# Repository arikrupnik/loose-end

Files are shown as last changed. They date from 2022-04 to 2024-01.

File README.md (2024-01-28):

# loose-end: Rocket Glider Research Program

I have a loose end I've been meaning to tie since 2012--a large R/C rocket glider.

Loose End is a family of aircraft.
I use OpenSCAD to define parametric models that can scale from parkflier to giant scale.
A goal of this project is to automate as much of the process as possible to allow for faster iteration of the design.
I use a Makefile to generate individual STLs from the master design, and g-code from the STLs.
Some parts (fins and wing joiner tabs) are in 1.6mm fiberglass (G10); the Makefile generates DXFs for them.

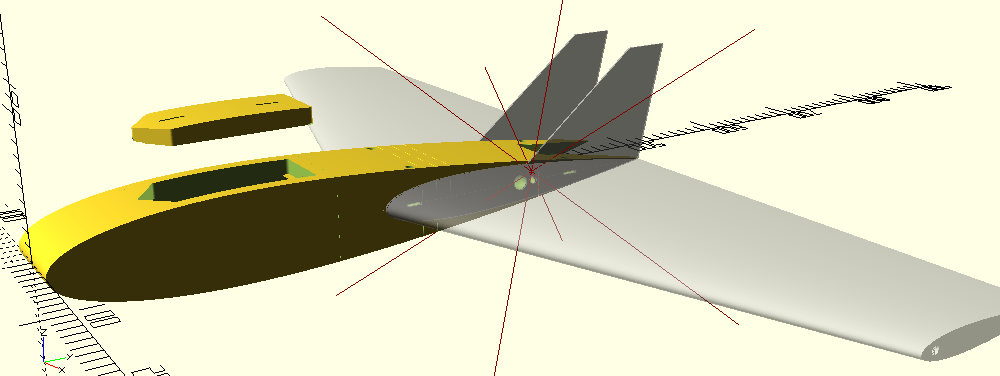
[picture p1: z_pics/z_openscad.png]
OpenSCAD model


Initial versions use off-the-shelf wings from a HobbyKing RadJet800.
This version has a 24mm motor mount.
This version has flown on E9, E15, E6, E20 and F12 motors.
In January 2023, I am designing printable wings.

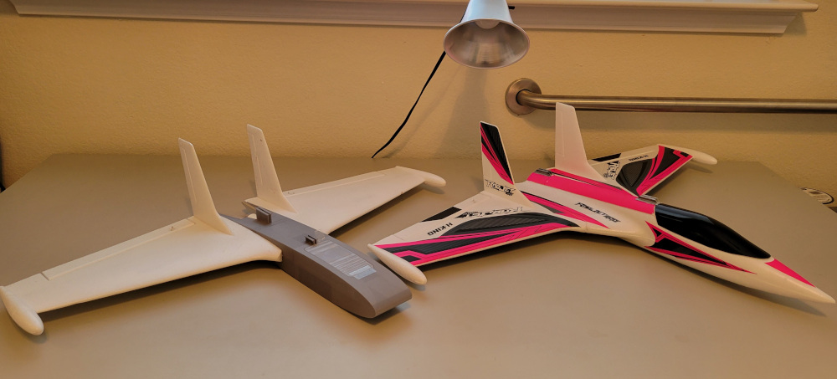
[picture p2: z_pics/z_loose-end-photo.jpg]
Loose End 24 and RadJet800


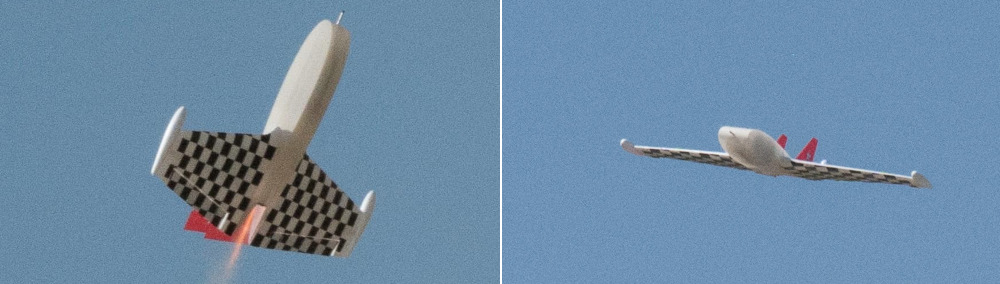
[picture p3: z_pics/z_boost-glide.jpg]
Loose End 24 DW in boost and glide


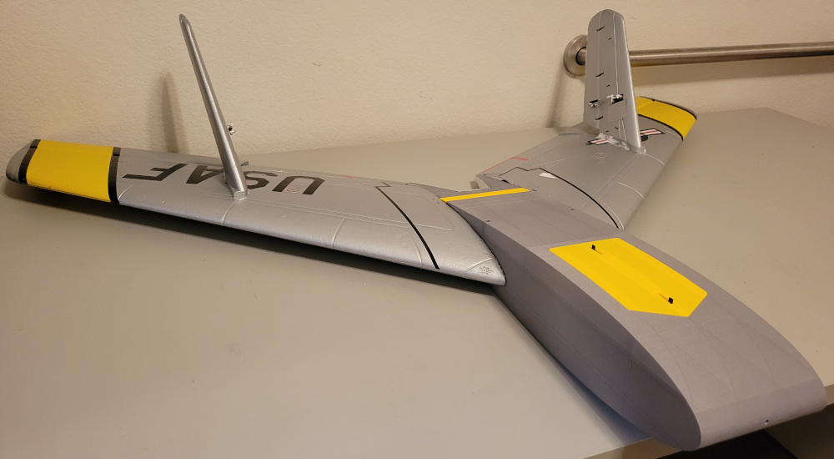
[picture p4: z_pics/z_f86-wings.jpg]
Loose End 29 using Freewing F-86 wings


Fuselage prints upright, in sections.
Most pieces use a single perimeter and 2% infill.
Spar carrythrough (green in the image below) uses 15% infill.
This part allows me to cut wing spar in two and the motor to pass through the wing, similar to mid-wing jet fighters like MiG-21 or F-16.

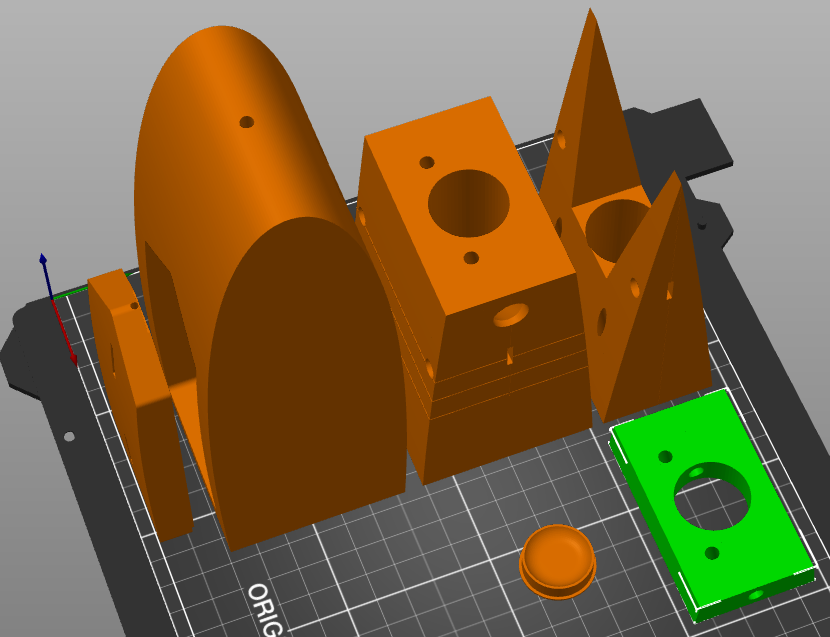
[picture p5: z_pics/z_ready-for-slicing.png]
Ready for Printing


I print these models on a Prusa MK3S+ using Prusament PLA.
I use PrusaSlicer in batch mode: [slicer-config](slicer-config) directory holds the INI files I use.
Key settings are:

* Most parts are single wall:
  * Perimeters: 1
  * Horizontal Shells: top: 3, bottom: 1 (max shell thickness bottom: 0 to force single layer)
  * Infill Density: 2%
  * Infill Pattern: Grid
  * Max Length of Infill Anchor: 0 (with some infill patterns, other values create arbitrarily long anchors; 3mm would be ideal)
  * Filament Extra Length on Retract: 0.1mm (helps avoid gaps between infill and perimeters)
  * Brim: outer, 3mm
* Spar carrythrough:
  * Perimeters: 2
  * Infill Density: 15%
  * Infill Pattern: Grid
  * Brim: outer, 3mm
* MMT plug:
  * Fill Pattern: concentric
  * Top Fill Pattern: concentric
  * Bottom Fill Pattern: concentric
  * Brim width: 0mm (the model has its own shoulder)

I make a new tag (release) when I print a new flying aircraft.
Release notes summarize changes from previous version and actual experience with them.

* January 2024: 29mm version using wings and fins from 80mm Freewing F-86
* October 2022: PLA fuselage, RJ wings, G10 fins
* April 2022: first flights, PLA fulseage, RJ wings and fins

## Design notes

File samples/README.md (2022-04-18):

# samples/: example usage for modules in this project

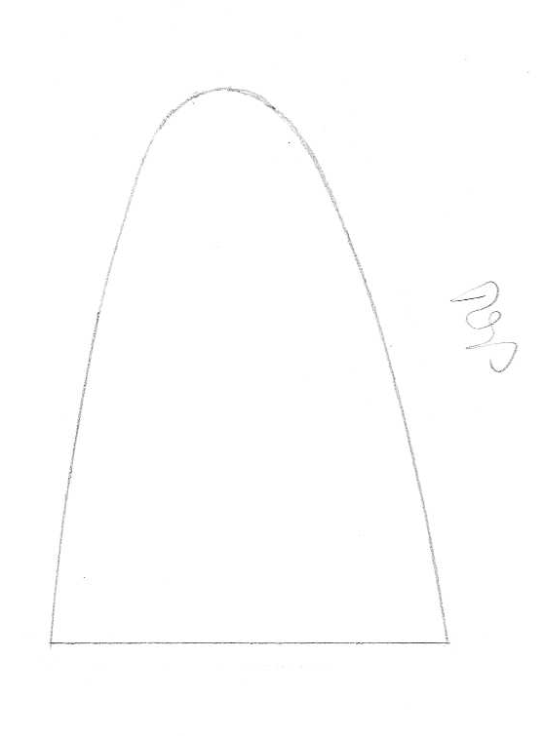
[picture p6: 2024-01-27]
extras/bronco-le.png

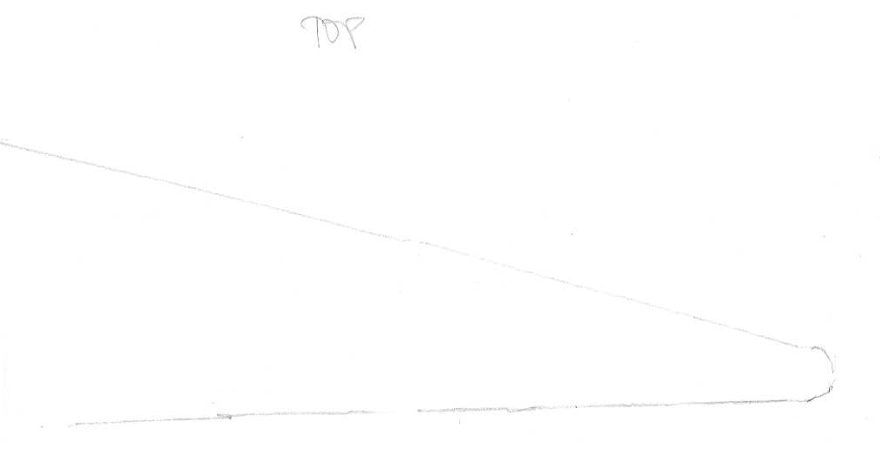
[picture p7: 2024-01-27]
extras/bronco-te.png

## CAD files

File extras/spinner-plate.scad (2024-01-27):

include <BOSL2/std.scad>

$fn=64;

difference() {
  up(0.5) {
    zcyl(d=94, h=5);}
  zcyl(d=10, h=7, circum=true);
  zcyl(d=90, h=4, anchor=BOTTOM);
  for(i = [0:30:360]) {
    zrot(i) {
      xmove(35) {
        zcyl(d=15, h=7);}
      zrot(15) {
        xmove(20) {
          zcyl(d=8, h=7);}}}}}

up(10)
difference() {
  zcyl(d=18, h=10);
  zcyl(d=10, h=10, circum=true);}

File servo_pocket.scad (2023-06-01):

// servo_pocket.scad: cutouts for servos


// the canonical definitions for these variables are in parameters.inc
LAYER_H = 0.15;
EXTRUSION_W = 0.45;

include <BOSL2/std.scad>
include <BOSL2/structs.scad>

/*
         _             _
        | |____       | |
     ==|       |==   |===|
  _^   |       |     |   | ^ (z=0 at bottom of tab)
 | v  _|       |     |   | h (from bottom of tab to bottom of servo)
 |     |_______|     |___| v
 |     |<- l ->|     |<w>|
 |   |<-l_w_tabs->|
 |
  \ wire exit (from bottom of tab to top of wire)

*/

// servo pocket where the servo shaft is normal to the surface in
// which it embeds

module servo_pocket_vertical(srv, projection_h=15) {
  let(w = struct_val(srv, "w"),
      l = struct_val(srv, "l"),
      h = struct_val(srv, "h"),
      l_w_tabs = struct_val(srv, "l_w_tabs"),
      wire_exit = struct_val(srv, "wire_exit")) {
    difference() {
      _servo_plug(w, l, h, l_w_tabs, wire_exit, projection_h);
      _servo_supports(w, l, h, l_w_tabs, wire_exit, projection_h);
    }
  }
}

module _servo_plug(w, l, h, l_w_tabs, wire_exit, projection_h) {
  // main body
  cube([w,l,h], anchor=FRONT+TOP);
  // tabs and their projection upward
  tab = (l_w_tabs - l) / 2;
  fwd(tab)
    cube([w, l_w_tabs, projection_h],
         anchor=FRONT+BOTTOM);
  // TODO: screw holes
  // clearance for wire during insertion
  let(wire_width = 4,
      wire_thick = 1.5)
    fwd(wire_thick)
          cube([wire_width, wire_thick, wire_thick+wire_exit],
               anchor=FRONT+TOP);
}

module _servo_supports(w, l, h, l_w_tabs, wire_exit, projection_h) {
  let(max_span_l = 5,
      num_spans = ceil(l / max_span_l),
      span_l = l / num_spans)
    up(projection_h)
      for(i=[span_l:span_l:l-span_l])
        back(i)
          cube([w-LAYER_H,  // to skip a layer on top and bottom
                EXTRUSION_W,  // single-wall-thick
                // not quite touching the inside wall
                h+projection_h-EXTRUSION_W/2],
               anchor=TOP);
}


function servo(w, l, h, l_w_tabs, wire_exit, typ_sink, tab_h) =
  struct_set([], ["w", w,
                  "l", l,
                  "h", h,
                  "l_w_tabs", l_w_tabs,
                  "wire_exit", wire_exit,
                  "typ_sink", typ_sink,
                  "tab_h", tab_h]);


// definitions for specific servos
SERVOS = struct_set([], ["HS-50", servo(w=11.5,
                                        l=21,
                                        h=14,
                                        l_w_tabs=30,
                                        wire_exit=9,
                                        typ_sink=5,
                                        tab_h=1.0),
                         "HS-55", servo(w=12,
                                        l=23.75,
                                        h=16.5,
                                        l_w_tabs=32.5,
                                        wire_exit=12,
                                        typ_sink=4,
                                        tab_h=1.2)]);

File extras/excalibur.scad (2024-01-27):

// excaliburd: rocket MMT for HobbyKing Excalibur warmliner

include <BOSL2/std.scad>
include <../airfoil.scad>

$fn=128;

SPAR_D_FRONT = 6.2; // front spar diameter
SPAR_D_REAR = 6.2;  // rear spar diameter
SPAR_CENTERS=29;    // distance between spars front-to-back
PYLON_CENTERS=20;   // distance between pylons, left-to-right
PYLON_H = 50;       // distance between MMT center and spar centers, top-to-bottom
MMT_ID = 31.7;      // cardboard tube OD, plastic tube ID (was 31.5, 32)
MMT_OD = MMT_ID+1;  // plastic tube OD
MMT_L = 120;        // cardboard tube length
NC_L = 40;          // nose cone length

module mmt_cutout() {
  zmove(-0.5) {
    zcyl(d=MMT_ID, l=MMT_L+1, circum=true, anchor=BOTTOM);}
}

module mmt() {
  zcyl(d=MMT_OD, l=MMT_L, circum=true, anchor=BOTTOM);
}

module pylon(mount_tab_th=2, margin=SPAR_D_FRONT+SPAR_D_REAR) {
  h = SPAR_CENTERS+margin*1.5;
  zmove(h/2) {
    difference() {
      union() {
        cube([mount_tab_th, margin*1.5, h],
             anchor=CENTER);
        cube([mount_tab_th, PYLON_H, h],
             anchor=CENTER+BACK);}
      for(c=[[-1,SPAR_D_REAR],[1,SPAR_D_FRONT]]) {
        zmove(c[0]*SPAR_CENTERS/2)
          xcyl(d=c[1], l=mount_tab_th*1.5, circum=true);}}}}

module nosecone() {
  af_l = NC_L/3*10;
  af_th = MMT_OD / af_l * 100;
  top_half() {
    zmove(NC_L) {
      rotate_extrude() {
        zrot(270) {
          difference() {
            polygon(filter(function(p) p.y>=0, airfoil(af_th, af_l)));
            polygon(filter(function(p) p.y>=0, airfoil(af_th, af_l, shave=1)));}}}}}}

difference() {
  union() {
    mmt();
    zmove(MMT_L) {
      nosecone();}
    for(p=[-0.5, 0.5]) {
      xmove(p*PYLON_CENTERS) {
        ymove(PYLON_H) {
          pylon();}}}}
  mmt_cutout();}

/*
  Perimeters: 1
  Seam Position: Rear

  Top Fill Pattern: Concentric

  Skirt Loops: 0
  Brim Width: 3mm
 */

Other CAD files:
extras/motor_plugs.scad
airfoil.scad
extras/ace-module-enclosure.scad
extras/apc-sport-adapter.scad
extras/bronco-le.scad
extras/bronco-te.scad
extras/fc_mount_plate.scad
extras/jawstand-bearing.scad
extras/neptune-ballast-mount.scad
extras/neptune-penetrator-adapter.scad
extras/neptune-plane-fwd.scad
extras/reptile-dragon-pod.scad
extras/stryker-q-guide.scad
fc_mount-sample.scad
fc_mount.scad
fins.scad
fuselage.scad
ground-camera/camera-mount.scad
ground-camera/lens-cap.scad
latch.scad
loose_end.scad
mmtbulkhead.scad
rail_guide-sample.scad
rail_guides.scad
samples/fc_mount-sample.scad
samples/latch-sample.scad
samples/rail_guide-sample.scad
samples/servo_pocket-sample.scad
samples/wing-sample.scad
samples/wing-tang-sample.scad
variants/loose_end_24.scad
variants/loose_end_f86.scad
variants/loose_end_rj.scad
wing-tang.scad
wing.scad

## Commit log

2022-04-11 as flown on 4/2/22
    [airfoil.scad, mmt-plug.scad, winger-fuse.3mf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]
2022-04-11 flight controller mount
    [fc_mount-sample.scad, fc_mount.scad]
2022-04-12 can spam
    [airfoil.scad]
2022-04-13 changing coordinate system so that right=starbord, back=back, top=away from ground while gliding
    [winger-fuse.scad]
2022-04-13 factoring out rail guides
    [rail_guide-sample.scad, rail_guides.scad, winger-fuse.scad]
2022-04-18 derivative variants
    [loose_end_24.scad, loose_end_rj.scad, mmt-plug-24.scad]
2022-04-18 moving sample usage into separate directory
    [fc_mount-sample.scad, rail_guide-sample.scad, wing-sample.scad]
2022-04-18 under certain conditions, can overshoot and produce slightly negative values for i, subsequently producing NaN for sqrt()
    [airfoil.scad]
2022-04-29 correct dimensions
    [loose_end_rj.scad]
2022-04-29 igniter wire tunnelss with ballpoint-pen springs
    [fuselage.scad]
2022-05-15 additional statistics
    [loose_end.scad]
2022-05-16 pitot tube
    [fuselage.scad]
2022-05-17 cockpit hatch latch
    [fuselage.scad, latch-sample.scad, latch.scad]
2022-05-17 wider hatch shelves
    [fuselage.scad]
2022-05-17 sharper point on hatch: to aid bridging
    [fuselage.scad]
2022-05-18 harder scribe lines
    [fuselage.scad, loose_end.scad]
2022-05-19 front and rear hatch latches
    [fuselage.scad]
2022-05-19 hatch shelf gap
    [fuselage.scad]
2022-05-21 wing tang with reinforcement ribs; tang slots for fuselage and fins
    [fuselage.scad, loose_end.scad, wing-tang-sample.scad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]
2022-05-22 correcting hatch hole
    [fuselage.scad]
2022-05-22 removing redundant definition of EPSILON
    [wing-tang.scad]
2022-05-26 smoother servo tunnels
    [fuselage.scad]
2022-05-26 small adjustments
    [wing-tang.scad]
2022-05-26 separating root rib from fin outline, to allow tang template
    [loose_end.scad]
2022-10-04 wider opening for screw head
    [wing-tang.scad]
2022-10-04 dimensions as flowin in May 2022
    [loose_end_rj.scad]
2022-10-04 as flowin in May 2022
    [fins.scad, fuselage.scad, loose_end.scad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]
2022-10-06 CG marks as positive relief
    [fuselage.scad]
2022-10-06 with additional depth to facilitate tapping without a blind tap
    [wing-tang.scad]
2022-10-12 longer (less hort) fuselage for CG
    [loose_end_rj.scad]
2022-10-26 remove CG marks from side of fuselage (interfere with root rib)
    [fuselage.scad]
2022-10-31 rail guide moves from top to bottom
    [fuselage.scad]
2022-10-31 more consistent formatting
    [fuselage.scad]
2022-12-10 adding missing parameters
    [wing-sample.scad]
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2022-12-21 moving airfoil functions into airfoil.scad
    [airfoil.scad, wing.scad]
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2022-12-22 airfoil is now a function and a module
    [airfoil.scad, wing.scad]
2022-12-22 spars are now children of wings
    [wing-sample.scad, wing.scad]
2022-12-22 defining wing in terms of skin rather than extrusion
    [wing.scad]
2022-12-22 all files use new wing/spar format
    [fins.scad, fuselage.scad, loose_end.scad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]
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2022-12-25 automatic g-code generation; automatic generation of separate STL files from one OpenSCAD model
    [fuselage.scad, loose_end.scad]
2022-12-26 motor mount bulkhead now part of loose_end*.scad; uses parameters.inc, displays as part of preview, generates own STL and g-code
    [loose_end.scad, mmt-plug-24.scad, mmt-plug.scad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]
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2022-12-30 airfoil generator now avoids duplicating points at 0% and 100% chord
    [airfoil.scad]
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2023-01-03 rudimentary wing shape with spar tube; working slicer configuration
    [loose_end.scad, wing.scad]
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2023-01-04 wing segmentation; separting generic wing functionality from LE-specific
    [airfoil.scad, loose_end.scad, wing-sample.scad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]
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2023-01-05 cleaning up flat parts
    [fin-projection.scad, loose_end.scad]
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2023-01-05 remove special case for symmetric airfoils, dependence on chord length from inner functions
    [airfoil.scad]
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2023-01-27 adding motor plugs, standalone flight contoller mount plate
    [fc_mount_plate.scad, motor_plugs.scad]
2023-01-27 wider cockpit to accommidate RX
    [fuselage.scad]
2023-01-30 initial servo pocket work
    [servo_pocket-sample.scad, servo_pocket.scad]
2023-01-30 wnig tangs on the wing side
    [wing-tang-sample.scad, wing-tang.scad, wing.scad]
2023-02-01 correcting fin airfoil, displacement of wing
    [fins.scad, loose_end.scad]
2023-02-02 refactoring servos as finctions
    [servo_pocket-sample.scad, servo_pocket.scad]
2023-02-04 fins are part of the build
    [loose_end.scad]
2023-02-04 generate left and right wings
    [wing.scad]
2023-02-04 servo pocket placement on wing
    [airfoil.scad, wing.scad]
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2023-05-30 replacement lower bearing for JawStand launcher; reduces wobble
    [jawstand-bearing.scad]
2023-05-30 Launcher guide for UMX Stryker; prevents rotation on launch rod
    [stryker-q-guide.scad]
2023-05-30 mount for ground camera, ZR10
    [camera-mount.scad, lens-cap.scad]
2023-05-30 plugs for 18mm motors
    [motor_plugs.scad]
2023-06-01 faster servo wire tunnels in fuselage
    [fuselage.scad]
2023-06-01 servo tunnels in wing
    [servo_pocket.scad, wing.scad]
2023-06-01 control over hinge cutout angle
    [airfoil.scad, wing-sample.scad, wing.scad]
2023-06-02 better parametrization of hinge dimensions
    [airfoil.scad, wing-sample.scad, wing.scad]
2023-06-04 spar cutout is circumscribed diameter
    [airfoil.scad]
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2023-06-04 'live' hingle too beefy in PLA
    [wing.scad]
2023-12-21 automatically rotate fuselage segments for printing
    [fuselage.scad]
2024-01-27 wing holders for OV-10 Bronco
    [bronco-le.scad, bronco-te.scad]
2024-01-27 parts for neptune submarine
    [neptune-ballast-mount.scad, neptune-penetrator-adapter.scad, neptune-plane-fwd.scad]
2024-01-27 JR module enclosure for ACE RF module
    [ace-module-enclosure.scad]
2024-01-27 piggy-back motor pods for v-tail gliders
    [excalibur.scad, reptile-dragon-pod.scad]
2024-01-27 spacer plate for fitting OV-10 cowlings
    [spinner-plate.scad]
2024-01-27 spartestblock for tesing spar and mmt fit
    [loose_end.scad]
2024-01-28 wing code works with 0 or more servos
    [loose_end_rj.scad, wing.scad]
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
